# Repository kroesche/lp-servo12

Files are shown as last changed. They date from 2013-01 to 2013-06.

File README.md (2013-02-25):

12-Servo BoosterPack for Stellaris Launchpad
============================================
by KROESCHE.ORG

---

License
-------
All documentation and design files including schematic and board layout is licensed under a Creative Commons Attribution 3.0 Unported License.

You should have received a copy of the license along with this work.  If not, see <http://creativecommons.org/licenses/by/3.0/>.

Please see the accompanying file LICENSE.TXT.

Summary
-------
This board is designed to be used with a Stellaris Launchpad.  It provides a power supply and connectors for 12 servos.  Each servo control signal can be driven from one half of a Stellaris Wide Timer.  The board is intended to be powered from a 2-cell LiPo battery pack and it will provide a 5-volt supply for the servos and optionally the Launchpad.

Power Supply
------------
The board is intended to be powered from a 2-cell LiPo battery pack or similar and can tolerate an input range of about 6-12V.  The onboard power supply will produce 5 volts with a current up to 5 amps.  The onboard supply can also be used to power the Stellaris Launchpad that is plugged in to the servo board. In order to do this, the jumper JP1 must be shorted.  By leaving this jumper open, you can choose to power the launchpad from a separate supply, either at J10 or through the Launchpad USB connector.

Battery Voltage Measurement
---------------------------
There is a circuit to allow for measurement of the battery supply voltage using the Stellaris A/D convertor.  It uses analog input signal AIN2.  It is scaled so that 6V supply reads 0 and 9V supply reads full scale.

Connectors
----------
* X1 - battery power supply, 6-12 V
* S0A - servo connector, uses wide timer 0A
* S0B - servo connector, uses wide timer 0B
* SnA/B - remaining servo connectors, using wide timer nA/B
* JP1 - short this jumper to supply Launchpad from the onboard supply
* J10 - can supply Launchpad 5V here if JP1 is left open
* J1-J4 - standard Launchpad connectors
* J5 - additional non-standard Launchpad connector needed for wide timer 4

Notes
-----
* If you want to use wide timer 4 (and you will if you want all 12 servos), you will need to add a stake-header connector to your Launchpad in the two holes next to the USB device connector.  You will not be able to use the USB device function if you use wide timer 4 for servo control.

* The board is intended to go under the Launchpad (LP sits on top), but there is no reason that it could not also plug on top of a LP.  It might cover some of the buttons on the top.

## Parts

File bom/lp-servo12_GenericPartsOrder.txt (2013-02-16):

Mfg Part Num	Mfg Name	VID	Vendor Part Num	Description	Customer Ref	Qty-1	Qty-5	Qty-25	Part References	Value
68002-110HLF	FCI	ME	649-68002-110HLF	Header, 0.1in, 10 pos, thru-hole	*	4	20	100	"J1, J2, J3, J4"	
68002-202HLF	FCI	ME	649-68002-202HLF	Header, 0.1in, 2 pos, thru-hole	*	2	10	50	"J5, JP1"	
68002-403HLF	FCI	ME	649-68002-403HLF	Header, 0.1in, 3 pos, thru-hole	*	12	60	300	"S0A, S0B, S1A, S1B, S2A, S2B, S3A, S3B, S4A, S4B, S5A, S5B"	
68016-402	FCI	ME	649-68016-402	Header, 0.1in, 2 pos, thru-hole, right-angle	*	1	5	25	"J10"	
KK-156-2-LOCK-RTANGLE	Molex	ME	538-26-61-5020	Molex, KK .156, Rt ang, 2-pin, lock (0026615020)	*	1	5	25	"X1"	
CAP_1u_20V_20PCT_0805	Murata	ME	81-GRM21BR71E105KA9K	Capacitor, 1uF, ceramic, 10%, 25V, 0805, X7R	*	6	30	150	"C4, C5, C6, C11, C13, C14"	1uF
IHLP3232DZER3R3M11	Vishay Dale	ME	70-IHLP3232DZER3R3M1	Inductor, 3.3uH, 20%, high current, low profile, 9.7A, 14.9mohm	*	1	5	25	"L1"	3.3uH
RES_10K_20V_1PCT_0805	Bourns	ME	652-CR0805FX-1002ELF	Resistor, 10K, 1%, 150V, 1/8W, 0805	*	3	15	75	"R17, R19, R21"	10K
CAP_10n_50V_10PCT_0805	Kemet	ME	80-C0805C103K5R	Capacitor, 10nF, 10%, 50V, 0805, X7R	*	1	5	25	"C12"	10nF
CAP_10u_20V_20PCT_1206	TDK	ME	810-C3216X7R1V106M	Capacitor, 10uF, ceramic, 20%, 35V, 1206, X7R	*	3	15	75	"C1, C2, C3"	10uF
RES_15K_20V_1PCT_0805	Bourns	ME	652-CR0805-FX1502ELF	Resistor, 15K, 1%, 150V, 1/8W, 0805	*	1	5	25	"R20"	15K
RES_22.1K_20V_1PCT_0805	Vishay Dale	ME	71-CRCW0805-22.1K-E3	Resistor, 22.1K, 1%, 150V, 1/8W, 0805	*	1	5	25	"R14"	22.1K
CAP_22p_50V_10PCT_0805	Kemet	ME	80-C0805C220J5G	Capacitor, 22pF, ceramic, 5%, 50V, 0805, C0G(NP0)	*	1	5	25	"C8"	22pF
CAP_22u_16V_10PCT_1210	Taiyo Yuden	ME	963-TMK325BJ226KM-T	Capacitor, 22uF, ceramic, 10%, 25V, 1210, X5R	*	1	5	25	"C9"	22uF
CAP_22u_16V_20PCT_1206	Murata	ME	81-GRM31CR61C226ME5L	Capacitor, 22uF, ceramic, 20%, 16V, 1206, X5R	*	1	5	25	"C10"	22uF
RES_30K_20V_1PCT_0805	Bourns	ME	652-CR0805FX-3002ELF	Resistor, 30K, 1%, 150V, 1/8W, 0805	*	2	10	50	"R16, R18"	30K
RES_100K_20V_1PCT_0805	Vishay Dale	ME	71-CRCW0805-100K-E3	Resistor, 100K, 1%, 150V, 1/8W, 0805	*	2	10	50	"R15, R22"	100K
CAP_100n_25V_10PCT_0805	AVX	ME	581-08053C104K	Capacitor, 100nF, ceramic, 10%, 25V, 0805, X7R	*	1	5	25	"C7"	100nF
RES_124K_20V_1PCT_0805	Vishay Dale	ME	71-CRCW0805124KFKEA	Resistor, 124K, 1%, 150V, 1/8W, 0805	*	1	5	25	"R13"	124K
RES_220_20V_10PCT_0805	Panasonic	ME	667ERJ-6GEYJ221V	Resistor, 220ohms, 5%, 150V, 1/8W, 0805	*	12	60	300	"R1, R2, R3, R4, R5, R6, R7, R8, R9, R10, R11, R12"	220
LMV358QDR	Texas Instruments	ME	595-LMV358QDR	Dual op-amp, low voltage, rail-to-rail	*	1	5	25	"U2"	LMV358
TPS54526PWP	Texas Instruments	ME	595-TPS54526PWP	DC/DC Switching Converter	*	1	5	25	"U1"	TPS54526PWP

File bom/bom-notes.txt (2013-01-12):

The script bom-ex.ulp was used to generate the BOM.

Files:
-----
lp-servo12_MouserOrder.txt - this file contains just quantities and mouser
part numbers

lp-servo12_GenericPartsOrder.txt - this file contains all of the BOM columns
that are produced by the bom-ex script, many of which are not useful.  This is
a tab-delimited file and you should be able to open it in a spreadsheet where
you can manipulate the columns to organize the data how you like.

bomex-partsdb.numbers - the original spreadsheet used to create the partsdb
used by bom-ex.

bomex-partsdb.txt - the partsdb from the spreadsheet, pasted into a text file.
This is the format needed by bom-ex.

Column meanings:
----------------
Mfg Part Num - this is actually the schematic attribute PARTNO and does not
necessarily represent the actual manufacturers part number.

Mfg Name - the name of the manufacturer of the part.  Of course for resistors
and capacitors, many manufacturers could be used.

VID - this is how bom-ex indicates the vendor - in this case ME means Mouser

Vendor Part Num - the actual part number to use for ordering from the vendor,
in this case Mouser

Description - a description of the part that is in the Vendor Part Num column

Customer Ref - not meaningful

Qty-1 - the number of parts to order for one board

Qty-5/Qty-25 - indicating number of parts to order for bulk orders (not used)

Part References - the schematic references for the parts

Value - the part value (if any) taken from the schematic

OTHER NOTES:
-----------
The 0.1in headers to not need to be ordered as discrete parts as shown in the
BOM list.  You can order the large length breakaway headers and cut them to the
length you ned.

The KK-156 battery connector (X1) could also be ordered as a kit that includes
the board header and the wire side housing and pins.  There is a kit for this,
p/n 76650-02208.  See also molexkits.com

The KK-156 (X1) connector specified is right angle but this could be replaced with
a straight connector instead.

The header J10 is optional.  This is not needed if you are not going to power
the launchpad separately from the servos.  Likewise JP1 does not need to be
populated if you want to keep the servo and launchpad supplies separate.

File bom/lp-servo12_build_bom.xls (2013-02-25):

Part References | Qty-1 | Mouser Part Num | Description | Value | Mfg Name | Mouser Qty-1 | Total Qty-1 | Mouser Qty-1000 | Total Qty-1000
J1, J2, J3, J4 | 4 | 649-68002-110HLF | Header, 0.1in, 10 pos, thru-hole |  | FCI | $0.43 | $1.72 | $0.298 | $1.192
J5, JP1 | 2 | 649-68002-202HLF | Header, 0.1in, 2 pos, thru-hole |  | FCI | $0.13 | $0.26 | $0.057 | $0.114
S0A, S0B, S1A, S1B, S2A, S2B, S3A, S3B, S4A, S4B, S5A, S5B | 12 | 649-68002-403HLF | Header, 0.1in, 3 pos, thru-hole |  | FCI | $0.12 | $1.44 | $0.080 | $0.960
J10 | 1 | 649-68016-402 | Header, 0.1in, 2 pos, thru-hole, right-angle |  | FCI | $0.10 | $0.10 | $0.057 | $0.057
X1 | 1 | 538-26-61-5020 | Molex, KK .156, Rt ang, 2-pin, lock (0026615020) |  | Molex | $1.59 | $1.59 | $0.670 | $0.670
C4, C5, C6, C11, C13, C14 | 6 | 81-GRM21BR71E105KA9K | Capacitor, 1uF, ceramic, 10%, 25V, 0805, X7R | 1uF | Murata | $0.15 | $0.90 | $0.044 | $0.264
L1 | 1 | 70-IHLP3232DZER3R3M1 | Inductor, 3.3uH, 20%, high current, low profile, 9.7A, 14.9mohm | 3.3uH | Vishay Dale | $1.33 | $1.33 | $0.740 | $0.740
R17, R19, R21 | 3 | 652-CR0805FX-1002ELF | Resistor, 10K, 1%, 150V, 1/8W, 0805 | 10K | Bourns | $0.05 | $0.15 | $0.020 | $0.060
C12 | 1 | 80-C0805C103K5R | Capacitor, 10nF, 10%, 50V, 0805, X7R | 10nF | Kemet | $0.10 | $0.10 | $0.008 | $0.008
C1, C2, C3 | 3 | 810-C3216X7R1V106M | Capacitor, 10uF, ceramic, 20%, 35V, 1206, X7R | 10uF | TDK | $0.35 | $1.05 | $0.202 | $0.606
R20 | 1 | 652-CR0805-FX1502ELF | Resistor, 15K, 1%, 150V, 1/8W, 0805 | 15K | Bourns | $0.05 | $0.05 | $0.020 | $0.020
R14 | 1 | 71-CRCW0805-22.1K-E3 | Resistor, 22.1K, 1%, 150V, 1/8W, 0805 | 22.1K | Vishay Dale | $0.08 | $0.08 | $0.018 | $0.018
C8 | 1 | 80-C0805C220J5G | Capacitor, 22pF, ceramic, 5%, 50V, 0805, C0G(NP0) | 22pF | Kemet | $0.10 | $0.10 | $0.012 | $0.012
C9 | 1 | 963-TMK325BJ226KM-T | Capacitor, 22uF, ceramic, 10%, 25V, 1210, X5R | 22uF | Taiyo Yuden | $1.09 | $1.09 | $0.302 | $0.302
C10 | 1 | 81-GRM31CR61C226ME5L | Capacitor, 22uF, ceramic, 20%, 16V, 1206, X5R | 22uF | Murata | $0.89 | $0.89 | $0.306 | $0.306
R16, R18 | 2 | 652-CR0805FX-3002ELF | Resistor, 30K, 1%, 150V, 1/8W, 0805 | 30K | Bourns | $0.05 | $0.10 | $0.020 | $0.040
R15, R22 | 2 | 71-CRCW0805-100K-E3 | Resistor, 100K, 1%, 150V, 1/8W, 0805 | 100K | Vishay Dale | $0.08 | $0.16 | $0.018 | $0.036
C7 | 1 | 581-08053C104K | Capacitor, 100nF, ceramic, 10%, 25V, 0805, X7R | 100nF | AVX | $0.10 | $0.10 | $0.027 | $0.027
R13 | 1 | 71-CRCW0805124KFKEA | Resistor, 124K, 1%, 150V, 1/8W, 0805 | 124K | Vishay Dale | $0.08 | $0.08 | $0.018 | $0.018
R1, R2, R3, R4, R5, R6, R7, R8, R9, R10, R11, R12 | 12 | 667ERJ-6GEYJ221V | Resistor, 220ohms, 5%, 150V, 1/8W, 0805 | 220 | Panasonic | $0.07 | $0.84 | $0.008 | $0.096
U2 | 1 | 595-LMV358QDR | Dual op-amp, low voltage, rail-to-rail | LMV358 | Texas Instruments | $0.59 | $0.59 | $0.275 | $0.275
U1 | 1 | 595-TPS54526PWP | DC/DC Switching Converter | TPS54526PWP | Texas Instruments | $5.13 | $5.13 | $2.570 | $2.570
PCB | 1 |  | LP-SERVO12 v1.1 PCB |  | OSH Park | $8.48 | $8.48 | $5.100 | $5.100
 |  |  |  |  |  | TOTAL | $26.33 |  | $13.491
NOTES:
Prices per Mouser 2013-02-16 (except for PCB)
Qty-1 PCB per OSH Park at $25.45 for 3 boards
Qty-1000 PCB price based on $1/sq in at OSH Park, actual volume mfr would be even lower

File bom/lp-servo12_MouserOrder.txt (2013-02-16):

649-68002-110HLF|4
649-68002-202HLF|2
649-68002-403HLF|12
649-68016-402|1
538-26-61-5020|1
81-GRM21BR71E105KA9K|6
70-IHLP3232DZER3R3M1|1
652-CR0805FX-1002ELF|3
80-C0805C103K5R|1
810-C3216X7R1V106M|3
652-CR0805-FX1502ELF|1
71-CRCW0805-22.1K-E3|1
80-C0805C220J5G|1
963-TMK325BJ226KM-T|1
81-GRM31CR61C226ME5L|1
652-CR0805FX-3002ELF|2
71-CRCW0805-100K-E3|2
581-08053C104K|1
71-CRCW0805124KFKEA|1
667ERJ-6GEYJ221V|12
595-LMV358QDR|1
595-TPS54526PWP|1

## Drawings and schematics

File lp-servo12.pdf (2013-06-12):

1

2

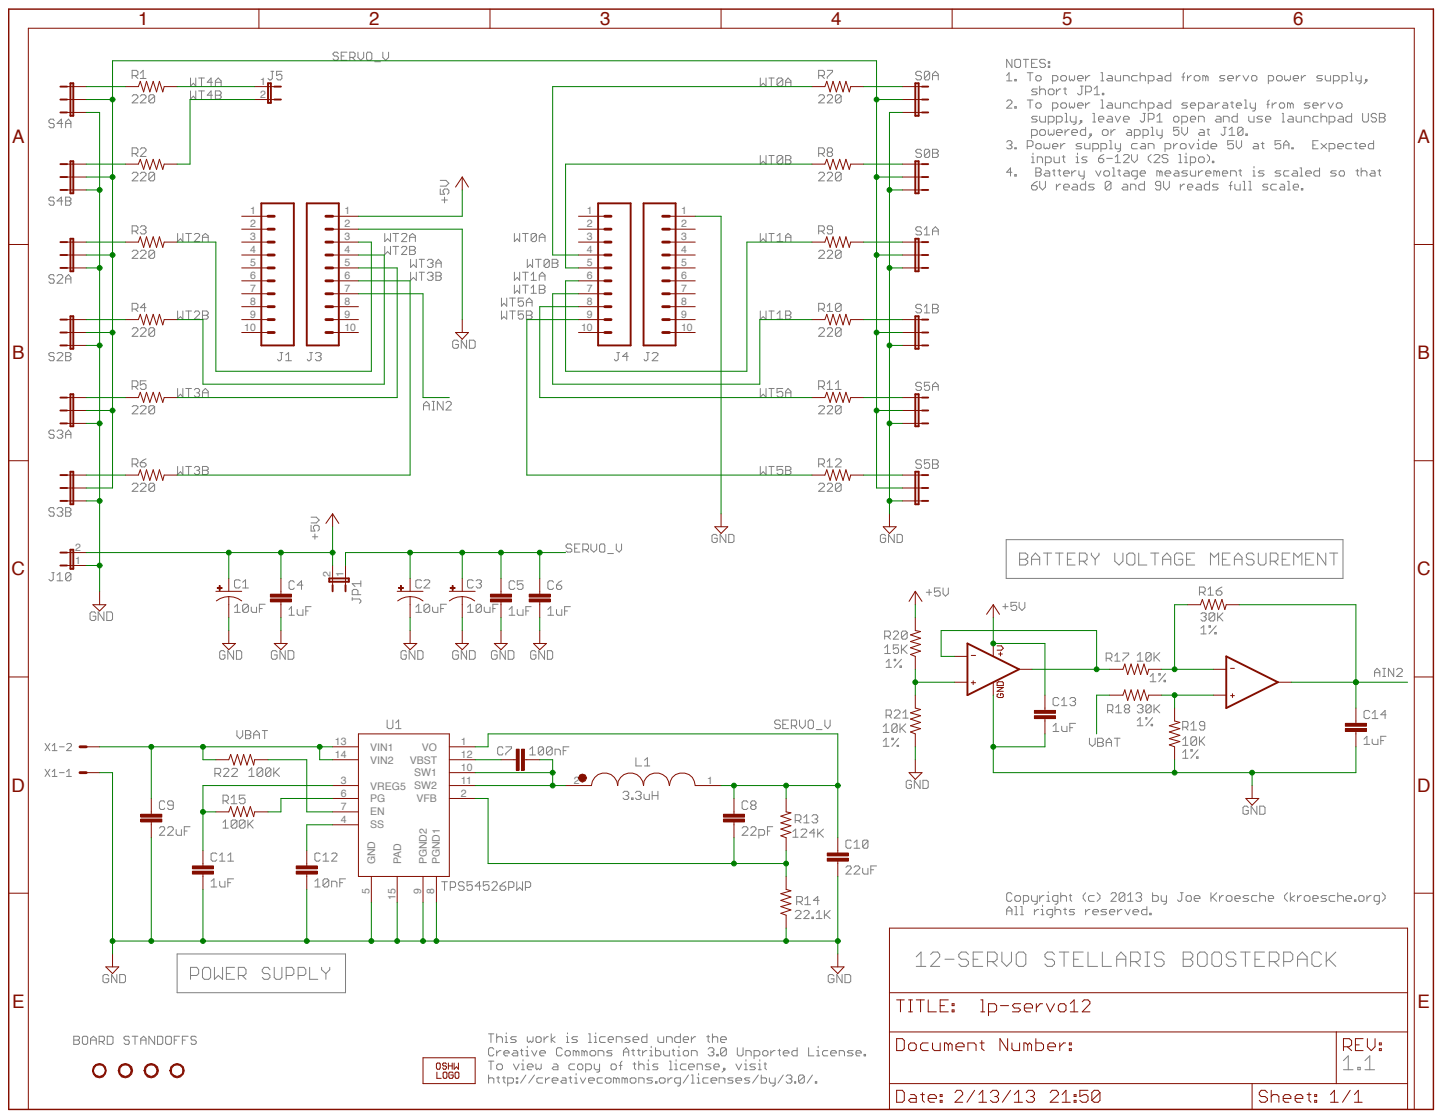
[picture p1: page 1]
VIN2 14; VIN1 13; VFB; GND 5; PGND2 9; PGND1 8; VREG5; VBST; PAD 15; ABCDE

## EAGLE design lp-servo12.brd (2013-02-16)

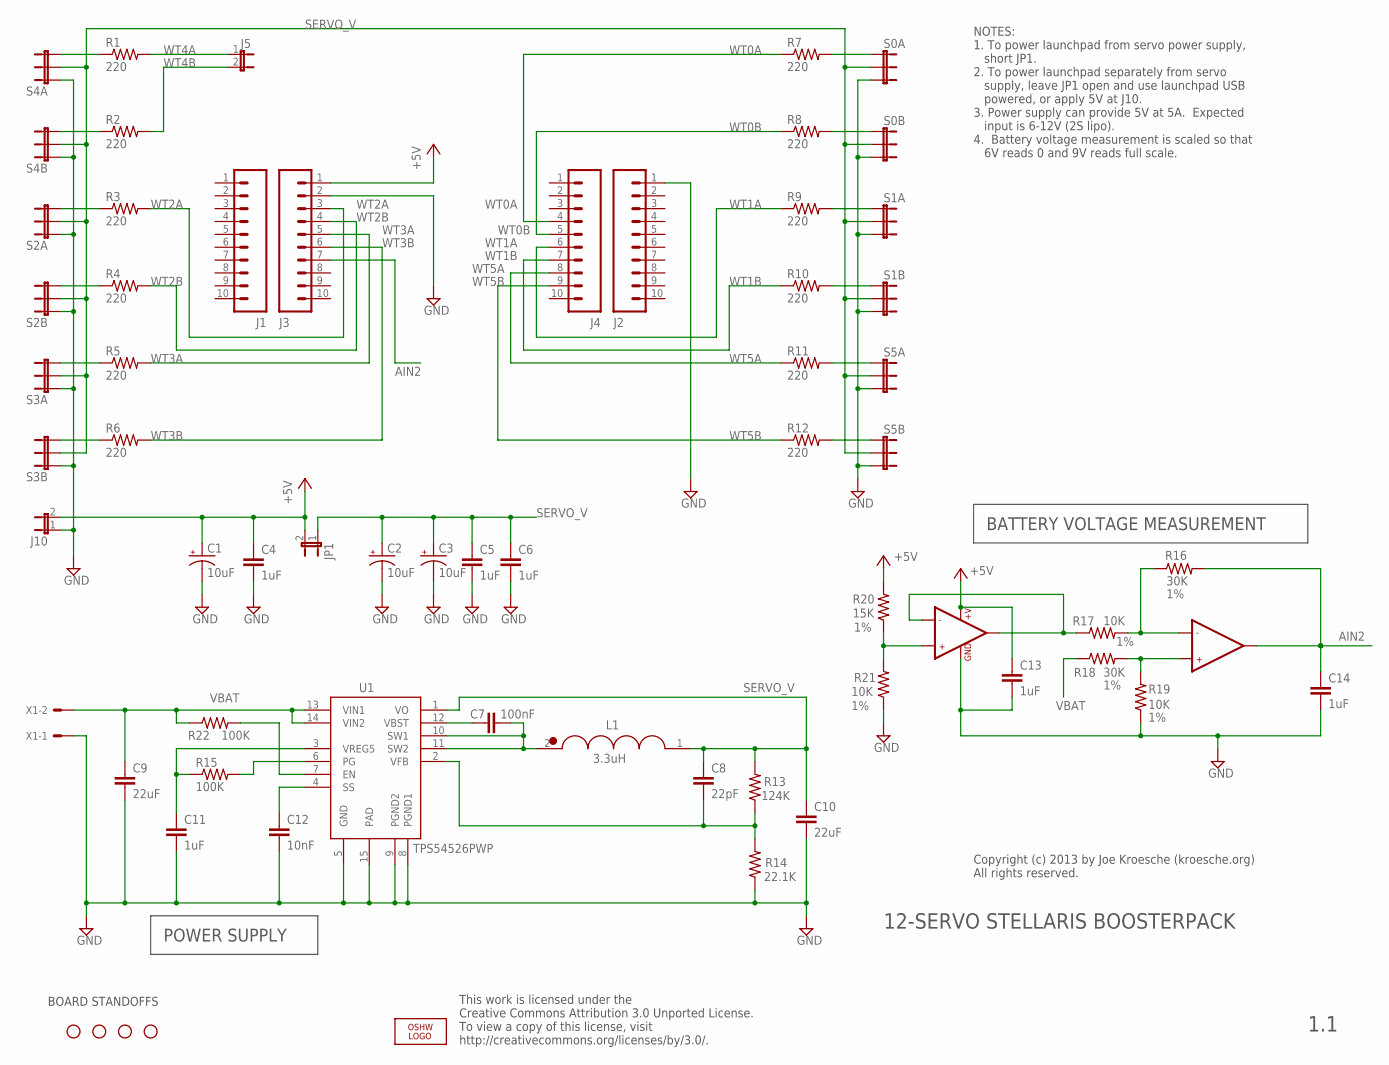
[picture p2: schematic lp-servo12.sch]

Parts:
C1, C2, C3: 10uF; EIA3216; PARTNO CAP_10u_20V_20PCT_1206
C4, C5, C6, C11, C13, C14: 1uF; 0805; PARTNO CAP_1u_20V_20PCT_0805
C7: 100nF; 0805; PARTNO CAP_100n_25V_10PCT_0805
C8: 22pF; 0805; PARTNO CAP_22p_50V_10PCT_0805
C9: 22uF; 1210; PARTNO CAP_22u_16V_10PCT_1210
C10: 22uF; 1206; PARTNO CAP_22u_16V_20PCT_1206
C12: 10nF; 0805; PARTNO CAP_10n_50V_10PCT_0805
J1, J2, J3, J4: M10"; 1X10; PARTNO 68002-110HLF
J5: JUMPER-2PTH; 1X02; PARTNO 68002-202HLF
J10: JUMPER-2PTH; 1X02; PARTNO 68016-402
JP1: JUMPER-2PTH; 1X02; PARTNO 68002-202HLF
L1: 3.3uH; VISHAY-IHLP3232DZER; MOUSER# 70-IHLP3232DZER3R3M11
LOGO2: OSHW_LOGO_6MILX0200-NT; OSHW_6X200_NOTEXT
R1: 220; 0805; MOUSER# 667-ERJ-6GEYJ221V
R2, R3, R4, R5, R6, R7, R8, R9, R10, R11, R12: 220; 0805; PARTNO RES_220_20V_10PCT_0805
R13: 124K; 0805; PARTNO RES_124K_20V_1PCT_0805
R14: 22.1K; 0805; PARTNO RES_22.1K_20V_1PCT_0805
R15, R22: 100K; 0805; PARTNO RES_100K_20V_1PCT_0805
R16, R18: 30K; 0805; PARTNO RES_30K_20V_1PCT_0805
R17, R19, R21: 10K; 0805; PARTNO RES_10K_20V_1PCT_0805
R20: 15K; 0805; PARTNO RES_15K_20V_1PCT_0805
S0A, S0B, S1A, S1B, S2A, S2B, S3A, S3B, S4A, S4B, S5A, S5B: JUMPER-3PTH; 1X03; PARTNO 68002-403HLF
STANDOFF1, STANDOFF2, STANDOFF3, STANDOFF4: STAND-OFF
U1: TPS54526PWP; PWP-R-PDSO-G14; PARTNO TPS54526PWP
U2: LMV358; SO08; MOUSER# 595-LMV358QDR
X1: KK-156-2; MOUSER# 538-76650-0208

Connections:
+5V: C1.A (+), C4.1, C13.1, J3.1, J10.2, JP1.2, R20.2, U2.8 (+V)
AIN2: C14.1, J3.7, R16.2, U2.7 (OUT2)
GND: C1.C (-), C2.C (-), C3.C (-), C4.2, C5.2, C6.2, C9.2, C10.2, C11.2, C12.2, C13.2, C14.2, J2.1, J3.2, J10.1, R14.1, R19.1, R21.1, S0A.3, S0B.3, S1A.3, S1B.3, S2A.1, S2B.1, S3A.1, S3B.1, S4A.1, S4B.1, S5A.3, S5B.3, U1.5 (GND), U1.8 (PGND1), U1.9 (PGND2), U1.15 (PAD), U2.4 (GND), X1.1
unnamed: R1.1, S4A.3
unnamed: C7.1, U1.12 (VBST)
unnamed: R2.1, S4B.3
unnamed: R3.1, S2A.3
unnamed: R4.1, S2B.3
unnamed: R5.1, S3A.3
unnamed: C7.2, L1.2 (POS), U1.10 (SW1), U1.11 (SW2)
unnamed: R16.1, R17.2, U2.6 (-IN2)
unnamed: R7.2, S0A.1
unnamed: R6.1, S3B.3
unnamed: R8.2, S0B.1
unnamed: R9.2, S1A.1
unnamed: R10.2, S1B.1
unnamed: R11.2, S5A.1
unnamed: R12.2, S5B.1
unnamed: C8.2, R13.1, R14.2, U1.2 (VFB)
unnamed: R18.2, R19.2, U2.5 (+IN2)
unnamed: R15.2, U1.6 (PG)
unnamed: R22.2, U1.7 (EN)
unnamed: C12.1, U1.4 (SS)
unnamed: R17.1, U2.1 (OUT1), U2.2 (-IN1)
unnamed: C11.1, R15.1, U1.3 (VREG5)
unnamed: R20.1, R21.2, U2.3 (+IN1)
SERVO_V: C2.A (+), C3.A (+), C5.1, C6.1, C8.1, C10.1, JP1.1, L1.1 (NEG), R13.2, S0A.2, S0B.2, S1A.2, S1B.2, S2A.2, S2B.2, S3A.2, S3B.2, S4A.2, S4B.2, S5A.2, S5B.2, U1.1 (VO)
VBAT: C9.1, R18.1, R22.1, U1.13 (VIN1), U1.14 (VIN2), X1.2
WT0A: J4.4, R7.1
WT0B: J4.5, R8.1
WT1A: J4.6, R9.1
WT1B: J4.7, R10.1
WT2A: J3.3, R3.2
WT2B: J3.4, R4.2
WT3A: J3.5, R5.2
WT3B: J3.6, R6.2
WT4A: J5.1, R1.2
WT4B: J5.2, R2.2
WT5A: J4.8, R11.1
WT5B: J4.9, R12.1

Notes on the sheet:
This work is licensed under the Creative Commons Attribution 3.0 Unported License. To view a copy of this license, visit http://creativecommons.org/licenses/by/3.0/.
Copyright (c) 2013 by Joe Kroesche (kroesche.org) All rights reserved.
BOARD STANDOFFS
BATTERY VOLTAGE MEASUREMENT
POWER SUPPLY
12-SERVO STELLARIS BOOSTERPACK
NOTES: 1. To power launchpad from servo power supply, short JP1. 2. To power launchpad separately from servo supply, leave JP1 open and use launchpad USB powered, or apply 5V at J10. 3. Power supply can provide 5V at 5A. Expected input is 6-12V (2S lipo). 4. Battery voltage measurement is scaled so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
1.1

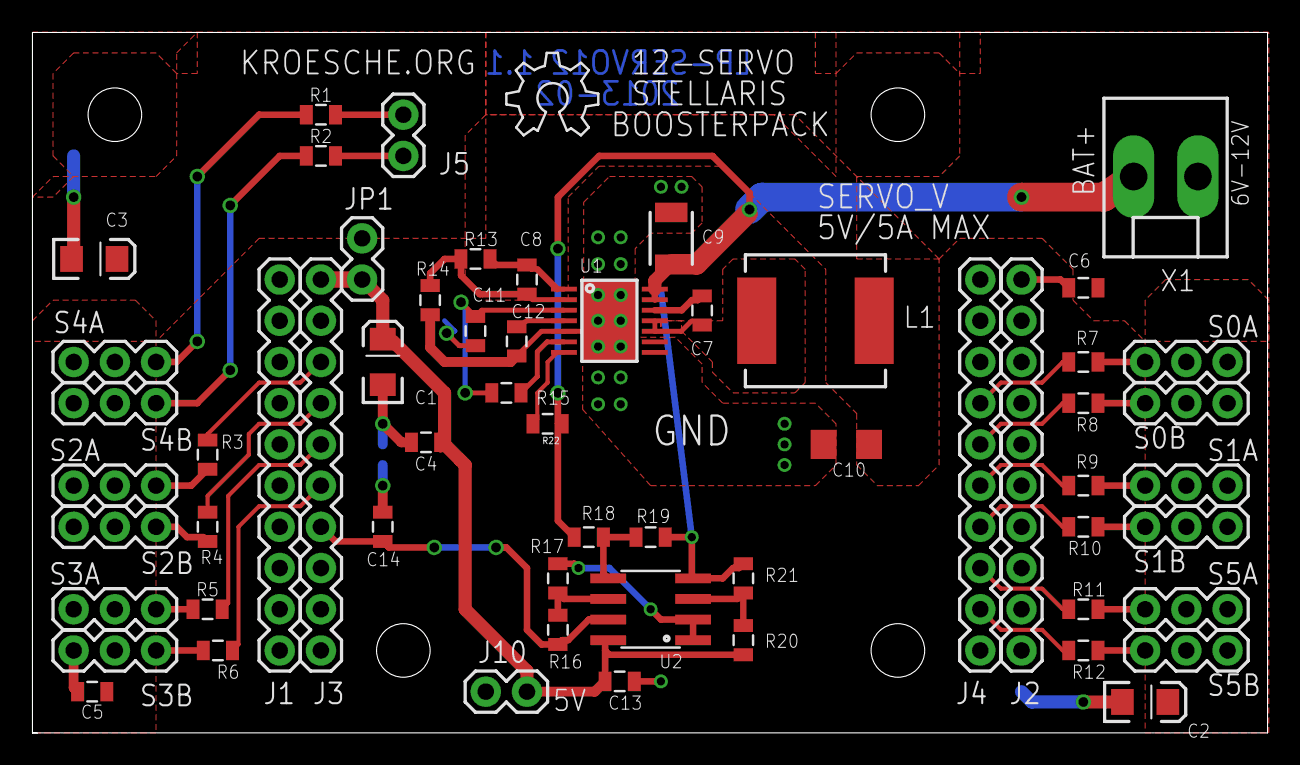
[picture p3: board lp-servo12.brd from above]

Board: 2 copper layers, 76.1 x 43.2 mm, 64 parts (0 on the bottom side), 40 nets.

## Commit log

2013-01-08 Initial commit of launchpad 12-servo board. This one seems complete and passes (most) design checks. (passes at batchpcb, some minor issues with freedfm)
    [servoboard.brd, servoboard.sch]
2013-01-08 Deleted the custom library since I put it in a common location. Renamed the source files to match the project name.
    [lp-servo12.brd, lp-servo12.sch]
2013-01-09 Close to final design. Board appears to pass all checks at batchpcb and OSHPark. May need a few more tweaks but really close to being done. The schematic could use some cleaning up for cosmetics. Add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
2013-01-09 Still learning git. All my files were not in the last commit.
    [lp-servo12.brd, lp-servo12.sch]
2013-01-09 Minor changes to layout. Moved battery connector so that mounting hole can go in the corner. Added notes to the bottom silkscreen.
    [lp-servo12.brd]
2013-01-10 Changed notes on back of board from one note with multiple lines to a separate text object for each line. This is because oshpark does not seem to handle multi-line text objects.
    [lp-servo12.brd]
2013-01-12 Updated schematic part attributes so that bom-ex script can be used to generate a BOM. Added parts database used and generated bom files (in bom/).
    [lp-servo12.brd, lp-servo12.sch]
2013-01-22 Added copyright and license text to board and schematic. Cosmetic changes only, no electrical or layout changes. Cleaned up schematic, added some comments. Change LICENSE to use creative commons attr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
    [lp-servo12.brd, lp-servo12.sch]
2013-01-22 Fixed some resistor values on the voltage measuring op-amp circuit. The orginal values were not correct for a 2S battery (they were for a 1S battery). Updated the bom files to reflect the changes in 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
    [lp-servo12.brd, lp-servo12.sch]
2013-02-16 Fixed missing pullup on enable line and unconnectd trace on feeback signal for power supply. Those were the two known bugs. Also moved one of the moounting holes and moved the power connector around 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
    [lp-servo12.brd, lp-servo12.sch]
2013-02-16 Updated generated BOM for revised board. The only change was increasing quantity of 100K resistor.
2013-02-25 Added build bom files, mainly for use in TI launchpad contest. This file shows all mouser part ordering info including qty-1 and qty-1000 pricing.
    [lp-servo12_build_bom.xls]
2013-02-25 Fixed battery voltage mistake text in README
2013-06-12 Added schematic PDF so it is easy to view schematic without needing Eagle.

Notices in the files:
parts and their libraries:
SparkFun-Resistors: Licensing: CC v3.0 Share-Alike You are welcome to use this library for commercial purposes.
